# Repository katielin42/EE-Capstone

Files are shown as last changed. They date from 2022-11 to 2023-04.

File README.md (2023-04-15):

# EE-Capstone
This repository is the master collection of technical files (excluding reports and posters) for ECE490/491 group 1 capstone - Formula SAE EVCU (electric vehicle control unit) project. Group members are enrolled in electrical engineering at the U of A. Our valuable consultant and helpers are staff and instructors of ECE 490/491 as well as Le Minh Dang, a computer engineering student, all of whom are from the University of Alberta as well. 

## Hardware
Below is a high level hardware block diagram describing our fabricated PCB. Detailed 3d-view of the PCB and schematic can be found under Hardware Design/EVCU Rev B/EVCU. 



Design created by: Thomas Osei-Bonsu Jr. and Katie Lin

## Software
Below is a high level software flowchart block diagram describing our software control flow. Detailed Documentation about code can be found below. We are using STM32Cube IDE to develop our code currently, so our configuration for our software has mostly been STM32Cube IDE presets.



Design created by: Katie Lin and Thomas Osei-Bonsu Jr.

**Libraries/modules/middlewares we used:** 

+ **FreeRTOS**: for scheduling tasks and other parallel programming functionalities

+ **FATFS**: for communications and r/w functions with the SD card

**Current code structure**:

```STM32_test.ioc```: Settings file for pin configurations, turning peripherials on/off with STM32Cube IDE...etc.

```main.c```: pin defines, generation of global tasks/mutexes/threads and starting the kernel. Also imports all the other functions and runs them. 

```SD_task.c && SD_task.h```: calls functions to perform r/w functions to and from sd card, as well as mount/dismount...etc. 

```ADC_task.c && ADC_task.h```: processes values going into ADC pins and saves them in an intermediate buffer for further logic/processing. 

```CAN_task.c && CAN_task.h```: processes operations relevant to STM32 BxCAN functionalities, such as sending and receiving CAN messages, encoding and decoding of such messages...etc. 

```controller_task.c && controller_task.h```: a giant state machine with cases, interrupts...etc that links all the tasks together. Based on the inputs and outputs of the task files described above, decide the next steps of what the MCU needs to do, usually sending CAN messages and error logging upon error detection. 

## User Manual (for EVCU PCB)

![image](https://user-images.githubusercontent.com/47064869/232248181-f159828e-b120-455e-b322-5c2face49e1b.png)

Above is a physical image of the EVCU PCB. 

**Hardware Setup**

The setup for EVCU PCB should be done after reviewing the schematic and layout, which can be found under Hardware Design/EVCU Rev B/EVCU. For the EVCU PCB, provide a 12v DC input at J2 and ground signal. 

At J3, the APPS VPA/VPA2 and BSE sensor signal inputs to the ADC are labelled. Please consult the accelerator pedal datasheets to hook the APPS pedal/BSE sensors up correctly. 

The J5 DB9 connector is the CAN connector that can be hooked up to the motor controller. Our CAN bus speed is 0.5Mbit/second, so configure the motor controller accordingly. 

Before powering the board up, please ensure a microSD card is inserted and the sensors are powered and operational and connected to the analog inputs of this PCB. The current firmware will start running once the board is powered up. If any firmware errors occur, disconnect the PCB from power, ensure the hardware components are all connected, and reconnect the PCB to power. 

**Firmware Setup**

If one wishes to modify the firmware, please download STM32CubeIDE and clone this repository. The firmware project name in this repository is STM32_Test. Then, hook up serial wire debug pins in J1 to a debug programmer. These configurations can be found online. Then, clicking on the run or debug button will flash the updated code onto the EVCU PCB MCU. 

+ If the error conditions for the analog APPS/BSE sensors need to be modified, they can be changed in controller_task.c under the function check_error_condition(). Currently the code checks for APPS/BSE <0.5 or >4.5V as specified by the rules, but I believe the datasheet for one of the sensors says otherwise. 
+ If any CAN address/settings need to be modified, they can be changed in CAN_task.c

**Caveats**
+ If SD card logs aren't removed after powering off the board, they will be wiped at the next instance the board is powered up. 
+ SD card cannot be removed in the middle of operation. 
+ SD card might die due to too many writes, just replace a new micro SD card if you notice the EVCU firmware behaving weirdly with the SD card. 

**The code also works with the dev board. However, several changes need to be made in the .ioc**
+ uSD_detect pin needs to be changed from PC7 to PA5. 
+ Clock configurations need to be set: HSE from BYPASS to crystal/ceramic oscillator, and disable LSE. 
+ Connect the CAN transciever module to the dev board via the USB breakout board, connect to the non ST-Link microUSB input on the dev board (there are only two). 

Finally, save those changes to the .ioc file, close it, and flash the code onto the dev board.

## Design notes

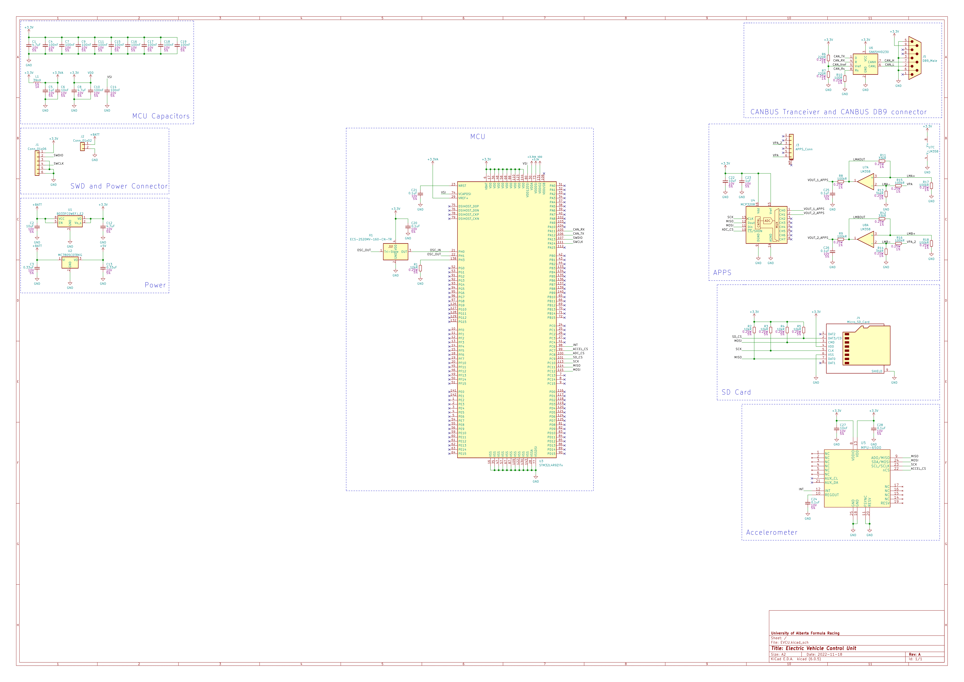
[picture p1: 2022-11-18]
Hardware Design/EVCU Rev B/EVCU.png

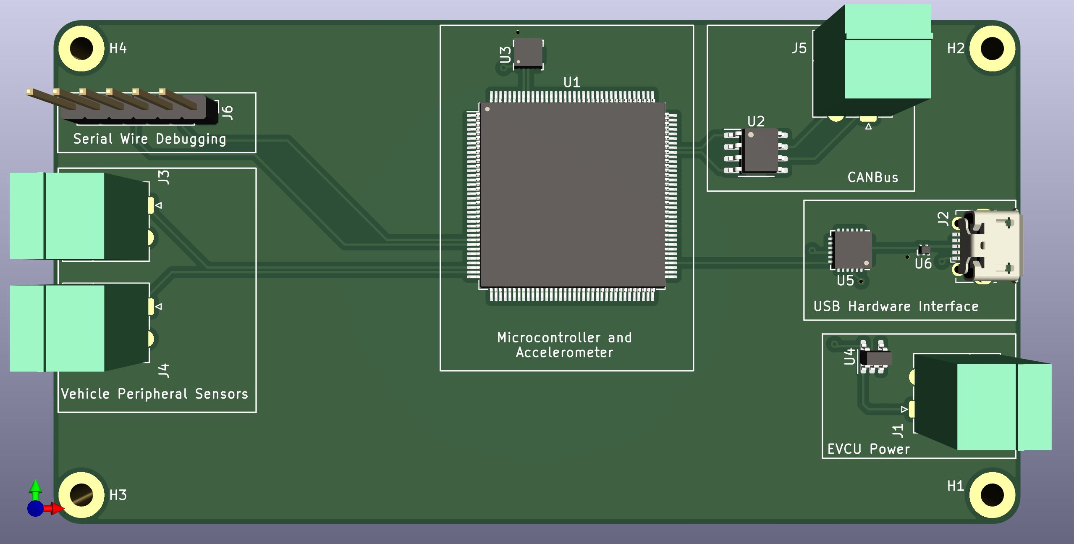
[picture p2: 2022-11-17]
3D Model/3DModelSpecificationsPictures/EVCUPic.png

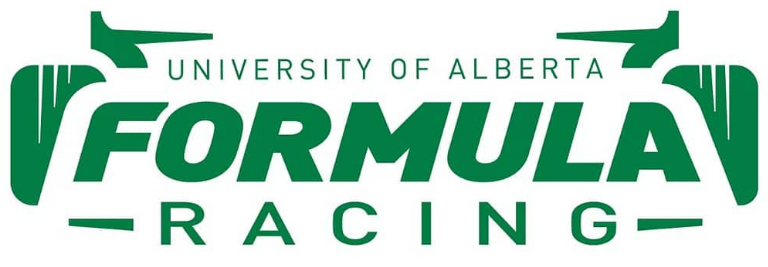
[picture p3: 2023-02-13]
3D Model/fsaepic.png

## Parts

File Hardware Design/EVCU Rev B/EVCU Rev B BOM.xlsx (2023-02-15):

Name | PCB Annotation | Value | Manufacturer | Mfr. P/N | Quantity | Description | Supplier | Supplier Link | Component Cost | Component Cost
STM32L4R9ZIT6 | U3 | IC MCU 32BIT 2MB FLASH 144LQFP | STMicroelectronics | STM32L4R9ZIT6 | 1 | ARM® Cortex®-M4 STM32L4R Microcontroller IC 32-Bit Single-Core 120MHz 2MB (2M x 8) FLASH 144-LQFP (20x20) | Digikey | https://www.digikey.ca/en/products/detail/stmicroelectronics/STM32L4R9ZIT6/7807676 | $35.44 | $118.61
AZ1117CR-3.3TRG1 | U1 | IC REG LINEAR 3.3V 1A SOT89 | Diodes Incorporated | AZ1117CR-3.3TRG1 | 1 | Linear Voltage Regulator IC Positive Fixed 1 Output 1A SOT-89-3 | Digikey | https://www.digikey.ca/en/products/detail/diodes-incorporated/AZ1117CR-3-3TRG1/4470988 | $0.69
AP62250WU-7 | U2 | DCDC CONV HV BUCK TSOT26 T&R 3K | Diodes Incorporated | AP62250WU-7 | 1 | Buck Switching Regulator IC Positive Adjustable 0.8V 1 Output 2.5A SOT-23-6 Thin, TSOT-23-6 | Digikey | https://www.digikey.ca/en/products/detail/diodes-incorporated/AP62250WU-7/12349212 | $0.77
ECS-2520MV-160-CN-TR | X1 | OSC XO 16.000MHZ CMOS SMD | ECS Inc. | ECS-2520MV-160-CN-TR | 1 | 16 MHz XO (Standard) HCMOS Oscillator 1.6V ~ 3.6V Enable/Disable 4-SMD, No Lead | Digikey | https://www.digikey.ca/en/products/detail/ecs-inc/ECS-2520MV-160-CN-TR/9742387 | $1.87
MPU-6500 | U5 | IMU ACCEL/GYRO 3-AXIS I2C 24QFN | TDK InvenSense | MPU-6500 | 1 | Accelerometer, Gyroscope, 6 Axis Sensor I²C, SPI Output | Digikey | https://www.digikey.ca/en/products/detail/tdk-invensense/MPU-6500/4385412 | $14.28
SN65HVD230QD | U6 | IC TRANSCEIVER HALF 1/1 8SOIC | Texas Instruments | SN65HVD230QDR | 1 | 1/1 Transceiver Half CANbus 8-SOIC | Digikey | https://www.digikey.ca/en/products/detail/texas-instruments/SN65HVD230QDR/1574499 | $4.79
LMV321WG-7 | U4, U7, U8 | IC OPAMP GP 1 CIRCUIT SOT25 | Diodes Incorporated | LMV321WG-7 | 3 | General Purpose Amplifier 1 Circuit Rail-to-Rail SOT-25 | Digikey | https://www.digikey.ca/en/products/detail/diodes-incorporated/LMV321WG-7/2182582 | $6.41
ESDCAN24-2BLY | U9 | TVS DIODE 24VWM 40VC SOT23-3 | STMicroelectronics | ESDCAN24-2BLY | 1 | 40V Clamp 5.5A (8/20µs) Ipp Tvs Diode Surface Mount SOT-23-3 | Digikey | https://www.digikey.ca/en/products/detail/stmicroelectronics/ESDCAN24-2BLY/3661709 | $0.71
EMIF06-MSD02N16 | U10 | FILTER RC(PI) 45 OHM/20PF SMD | STMicroelectronics | EMIF06-MSD02N16 | 1 | RC (Pi) EMI Filter 2nd Order Low Pass 6 Channel R = 45Ohms, C = 20pF (Total) 16-UFDFN Exposed Pad | Digikey | https://www.digikey.ca/en/products/detail/stmicroelectronics/EMIF06-MSD02N16/2043592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 | $1.76
ESDALC6V1W5 | U11 | TVS DIODE 3VWM SOT323-5 | STMicroelectronics | ESDALC6V1W5 | 1 | Clamp Ipp Tvs Diode Surface Mount SOT-323-5 | Digikey | https://www.digikey.ca/en/products/detail/stmicroelectronics/ESDALC6V1W5/1037997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 | $0.79
PJA3405_R1_00001 | Q1 | SOT-23, MOSFET | Panjit International Inc. | PJA3405_R1_00001 | 1 | P-Channel 30 V 3.6A (Ta) 1.25W (Ta) Surface Mount SOT-23 | Digikey | https://www.digikey.ca/en/products/detail/panjit-international-inc/PJA3405-R1-00001/14660219 | $0.71
0287001.PXCN | F1 | FUSE AUTO 1A 32VDC BLADE | Littelfuse Inc. | 0287001.PXCN | 1 | 1 A AC 32 V DC Fuse Automotive Requires Holder Blade, ATO/ATC | Digikey | https://www.digikey.ca/en/products/detail/littelfuse-inc/0287001-PXCN/3102551 | $0.48
3557_02 | F1 | FUSE BLOCK BLADE 500V 30A PCB | Keystone Electronics | 3557_02 | 1 | Fuse Block 30 A 500V 1 Circuit Blade Through Hole | Digikey | https://www.digikey.ca/en/products/detail/keystone-electronics/3557-2/2137305 | $2.09
SMBJ3V3-E3/5B | D1 | TVS DIODE 3.3VWM 10.3VC DO214AA | Vishay General Semiconductor - Diodes Division | SMBJ3V3-E3/5B | 1 | 10.3V Clamp 200A (8/20µs) Ipp Tvs Diode Surface Mount DO-214AA (SMBJ) | Digikey | https://www.digikey.ca/en/products/detail/vishay-general-semiconductor-diodes-division/SMBJ3V3-E3-5B/2147834 | $0.76
VJ0603Y104JXQPW1BC | C4, C7, C9, C10, C11, C15, C16, C17, C18, C19, C22, C31, C33, C20, C24, C25, C26, C28, C29, C30 | CAP CER 0.1UF 10V X7R 0603 | Vishay Vitramon | VJ0603Y104JXQPW1BC | 21 | 0.1 µF ±5% 10V Ceramic Capacitor X7R 0603 (1608 Metric) | Digikey | https://www.digikey.ca/en/products/detail/vishay-vitramon/VJ0603Y104JXQPW1BC/8305311 | $5.48
CL10A475KP8NNNC | C1, C8 | CAP CER 4.7UF 10V X5R 0603 | Samsung Electro-Mechanics | CL10A475KP8NNNC | 2 | 4.7 µF ±10% 10V Ceramic Capacitor X5R 0603 (1608 Metric) | Digikey | https://www.digikey.ca/en/products/detail/samsung-electro-mechanics/CL10A475KP8NNNC/3886702 | $1.70
CL31A106MBHNNNE | C3 | CAP CER 10UF 50V X5R 1206 | Samsung Electro-Mechanics | CL31A106MBHNNNE | 1 | 10 µF ±20% 50V Ceramic Capacitor X5R 1206 (3216 Metric) | Digikey | https://www.digikey.ca/en/products/detail/samsung-electro-mechanics/CL31A106MBHNNNE/5961220 | $2.69
CL10A106MA8NRNC | C2 | 10 µF ±20% 25V Ceramic Capacitor X5R 0603 (1608 Metric) | Samsung Electro-Mechanics | CL10A106MA8NRNC | 1 | 10 µF ±20% 25V Ceramic Capacitor X5R 0603 (1608 Metric) | Digikey | https://www.digikey.ca/en/products/detail/samsung-electro-mechanics/CL10A106MA8NRNC/3887527 | $2.58
CL10B105KP8NNNC | C5, C32 | CAP CER 1UF 10V X7R 0603 | Samsung Electro-Mechanics | CL10B105KP8NNNC | 2 | 1 µF ±10% 10V Ceramic Capacitor X7R 0603 (1608 Metric) | Digikey | https://www.digikey.ca/en/products/detail/samsung-electro-mechanics/CL10B105KP8NNNC/3887604 | $0.55
C1608X5R1A226M080AC | C13, C23, C12 | CAP CER 22UF 10V X5R 0603 | TDK Corporation | C1608X5R1A226M080AC | 3 | 22 µF ±20% 10V Ceramic Capacitor X5R 0603 (1608 Metric) | Digikey | https://www.digikey.ca/en/products/detail/tdk-corporation/C1608X5R1A226M080AC/3661560 | $4.51
GRM188R71A225KE15D | C14 | CAP CER 2.2UF 10V X7R 0603 | Murata Electronics | GRM188R71A225KE15D | 1 | 2.2 µF ±10% 10V Ceramic Capacitor X7R 0603 (1608 Metric) | Digikey | https://www.digikey.ca/en/products/detail/murata-electronics/GRM188R71A225KE15D/1033256 | $1.41
885012206014 | C6, C27 | CAP CER 10000PF 10V X7R 0603 | Würth Elektronik | 885012206014 | 2 | 10000 pF ±10% 10V Ceramic Capacitor X7R 0603 (1608 Metric) | Digikey | https://www.digikey.ca/en/products/detail/w%C3%BCrth-elektronik/885012206014/5453788 | $0.33
36502C39NJTDG | L1 | FIXED IND 100NH 8A 8 MOHM SMD | TDK Corporation | TFM322512ALMAR10MTAA | 1 | 100 nH Unshielded Thin Film Inductor 8 A 8mOhm Max 1210 (3225 Metric) | Digikey | https://www.digikey.ca/en/products/detail/tdk-corporation/TFM322512ALMAR10MTAA/16754576 | $2.98
CIGT252010EH2R2MNE | L2 | FIXED IND 2.2UH 2.4A 80MOHM SMD | Samsung Electro-Mechanics | CIGT252010EH2R2MNE | 1 | 2.2 µH Unshielded Thin Film Inductor 2.4 A 80mOhm Max 1008 (2520 Metric) | Digikey | https://www.digikey.ca/en/products/detail/samsung-electro-mechanics/CIGT252010EH2R2MNE/7041252 | $0.80
RNCP0805FTD10K0 | R1, R3 | RES 10K OHM 1% 1/4W 0805 | Stackpole Electronics Inc | RNCP0805FTD10K0 | 2 | 10 kOhms ±1% 0.25W, 1/4W Chip Resistor 0805 (2012 Metric) Anti-Sulfur Thin Film | Digikey | https://www.digikey.ca/en/products/detail/stackpole-electronics-inc/RNCP0805FTD10K0/2240262 | $1.12
ERJ-6ENF5232V | R2 | RES SMD 52.3K OHM 1% 1/8W 0805 | Panasonic Electronic Components | ERJ-6ENF5232V | 1 | 52.3 kOhms ±1% 0.125W, 1/8W Chip Resistor 0805 (2012 Metric) Automotive AEC-Q200 Thick Film | Digikey | https://www.digikey.ca/en/products/detail/panasonic-electronic-components/ERJ-6ENF5232V/111615 | $1.41
RK73H2ATTD2200F | R6, R7 | RES 220 OHM 1% 1/4W 0805 | KOA Speer Electronics, Inc. | RK73H2ATTD2200F | 2 | 220 Ohms ±1% 0.25W, 1/4W Chip Resistor 0805 (2012 Metric) Automotive AEC-Q200, Moisture Resistant Thick Film | Digikey | https://www.digikey.ca/en/products/detail/koa-speer-electronics-inc/RK73H2ATTD2200F/10234286 | $0.60
AC0805FR-7W100KL | R5, R9, R12 | RES 100 KOHM 1% 1/4W 0805 | YAGEO | AC0805FR-7W100KL | 9 | 100 kOhms ±1% 0.25W, 1/4W Chip Resistor 0805 (2012 Metric) Automotive AEC-Q200, Moisture Resistant Thick Film | Digikey | https://www.digikey.ca/en/products/detail/yageo/AC0805FR-7W100KL/12698912 | $1.14
RNCP0805FTD100R | R10 | RES 100 OHM 1% 1/4W 0805 | Stackpole Electronics Inc | RNCP0805FTD100R | 1 | 100 Ohms ±1% 0.25W, 1/4W Chip Resistor 0805 (2012 Metric) Anti-Sulfur Thin Film | Digikey | https://www.digikey.ca/en/products/detail/stackpole-electronics-inc/RNCP0805FTD100R/2240209 | $1.12
RC0805JR-0751KL | R4, R11, R8 | RES 51K OHM 5% 1/8W 0805 | YAGEO | RC0805JR-0751KL | 3 | 51 kOhms ±5% 0.125W, 1/8W Chip Resistor 0805 (2012 Metric) Moisture Resistant Thick Film | Digikey | https://www.digikey.ca/en/products/detail/yageo/RC0805JR-0751KL/728346 | $0.43
RK73B2ATTD121J | R19 | RES 120 OHM 5% 1/4W 0805 | KOA Speer Electronics, Inc. | RK73B2ATTD121J | 1 | 120 Ohms ±5% 0.25W, 1/4W Chip Resistor 0805 (2012 Metric) Automotive AEC-Q200 Thick Film | Digikey | https://www.digikey.ca/en/products/detail/koa-speer-electronics-inc/RK73B2ATTD121J/10236600 | $0.49
PPPC061LFBN-RC | J1 | CONN HDR 6POS 0.1 GOLD PCB | Sullins Connector Solutions | PPPC061LFBN-RC | 2 | 6 Position Header Connector 0.100" (2.54mm) Through Hole Gold | Digikey | https://www.digikey.ca/en/products/detail/sullins-connector-solutions/PPPC061LFBN-RC/810178 | $1.52
1984659 | J3 | TERM BLK 6POS SIDE ENT 3.5MM PCB | Phoenix Contact | 1984659 | 1 | 6 Position Wire to Board Terminal Block Horizontal with Board 0.138" (3.50mm) Through Hole | Digikey | https://www.digikey.ca/en/products/detail/phoenix-contact/1984659/950852 | $5.08
61300211121 | J6 | CONN HEADER VERT 2POS 2.54MM | Würth Elektronik | 61300211121 | 1 | Connector Header Through Hole 2 position 0.100" (2.54mm) | Digikey | https://www.digikey.ca/en/products/detail/w%C3%BCrth-elektronik/61300211121/4846823 | $1.63
1984617 | J2 | TERM BLK 2POS SIDE ENT 3.5MM PCB | Phoenix Contact | 1984617 | 2 | 2 Position Wire to Board Terminal Block Horizontal with Board 0.138" (3.50mm) Through Hole | Digikey | https://www.digikey.ca/en/products/detail/phoenix-contact/1984617/950849 | $3.44
693072010801 | J4 | CONN MICRO SD CARD HINGED TYPE | Würth Elektronik | 693072010801 | 1 | 8 Position Card Connector Secure Digital - microSD™ Surface Mount, Right Angle Gold | Digikey | https://www.digikey.ca/en/products/detail/w%C3%BCrth-elektronik/693072010801/3124584 | $4.91
A-DS 09 A/KG-T4S | J5 | CONN D-SUB PLUG 9POS R/A SLDR | Assmann WSW Components | A-DS 09 A/KG-T4S | 1 | 9 Position D-Sub Plug, Male Pins Connector | Digikey | https://www.digikey.ca/en/products/detail/assmann-wsw-components/A-DS-09-A-KG-T4S/1241806 | $1.14

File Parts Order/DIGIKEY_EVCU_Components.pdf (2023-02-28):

Please wait...

If this message is not eventually replaced by the proper contents of the document, your PDF viewer may not be able to display this type of document.

You can upgrade to the latest version of Adobe Reader for Windows®, Mac, or Linux® by visiting http://www.adobe.com/go/reader_download.

For more assistance with Adobe Reader visit http://www.adobe.com/go/acrreader.

Windows is either a registered trademark or a trademark of Microsoft Corporation in the United States and/or other countries. Mac is a trademark of Apple Inc., registered in the United States and other countries. Linux is the registered trademark of Linus Torvalds in the U.S. and other countries.

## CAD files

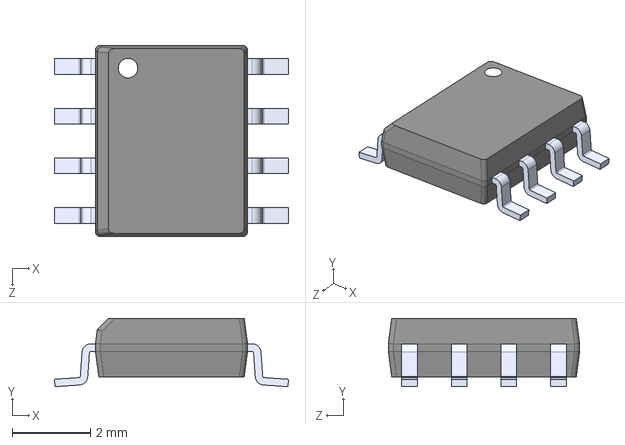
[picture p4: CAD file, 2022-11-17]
Hardware Design/KiCAD Custom Symbol Libraries/CAN-SN65HVD230/SN65HVD230.step
5.99 x 1.75 x 4.90 mm

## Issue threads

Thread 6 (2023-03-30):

ADC Value Scaling

katielin42, 2023-03-30:
Need to rescale ADC value from voltage divider 0-3.3v back to 0-5v

katielin42, 2023-04-10:
implemented fix, closing now

Closed 2023-04-10.

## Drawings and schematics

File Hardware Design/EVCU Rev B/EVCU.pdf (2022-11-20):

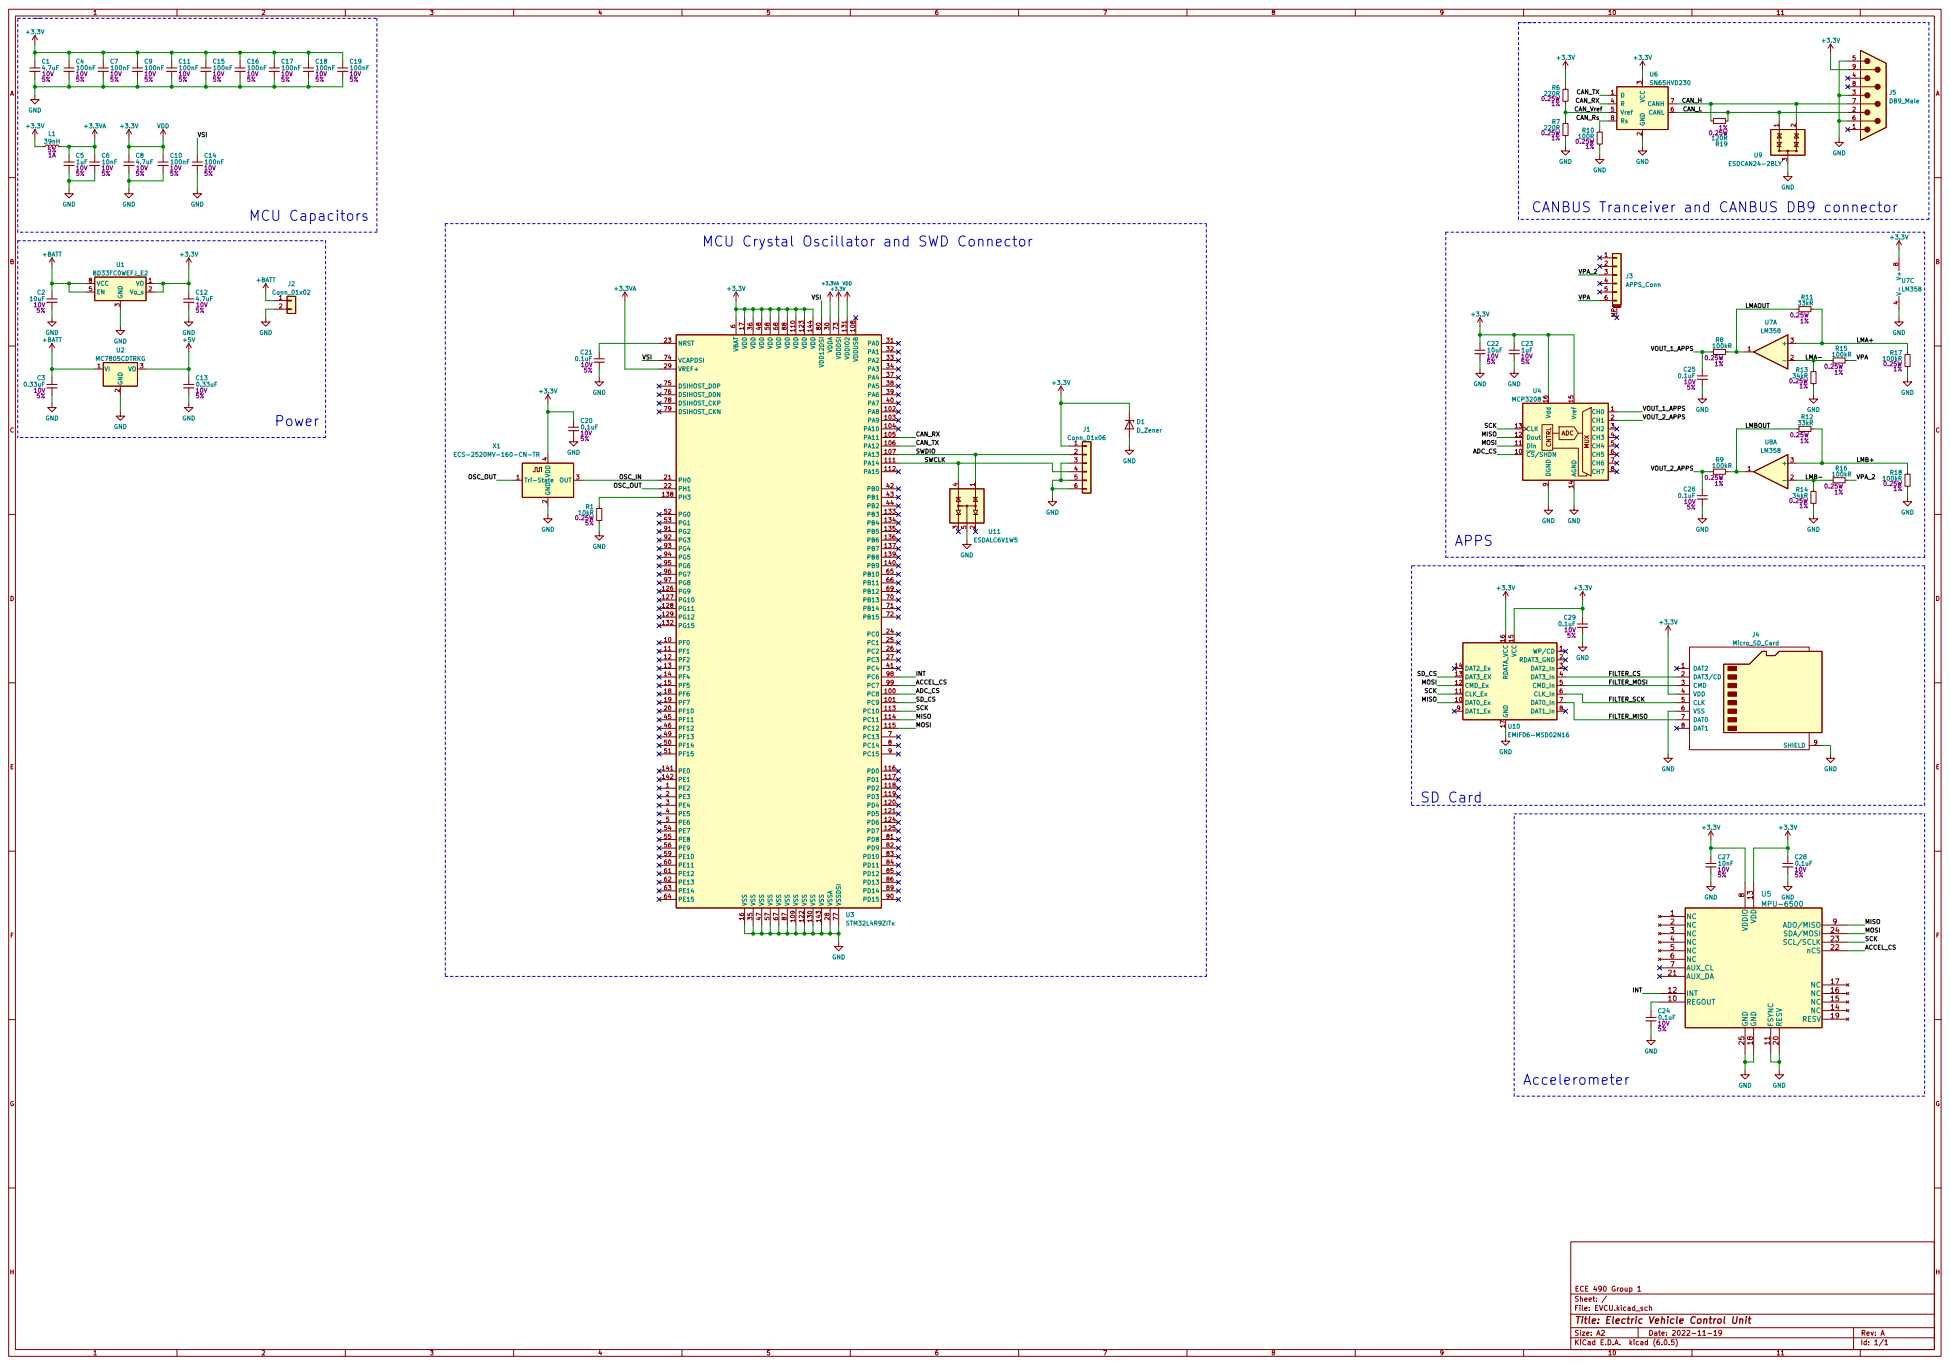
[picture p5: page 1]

CANBUS Tranceiver and CANBUS DB9 connector

MCU Crystal Oscillator and SWD Connector

File: EVCU.kicad_sch Sheet: / ECE 490 Group 1

Id: 1/1 Title: Electric Vehicle Control Unit

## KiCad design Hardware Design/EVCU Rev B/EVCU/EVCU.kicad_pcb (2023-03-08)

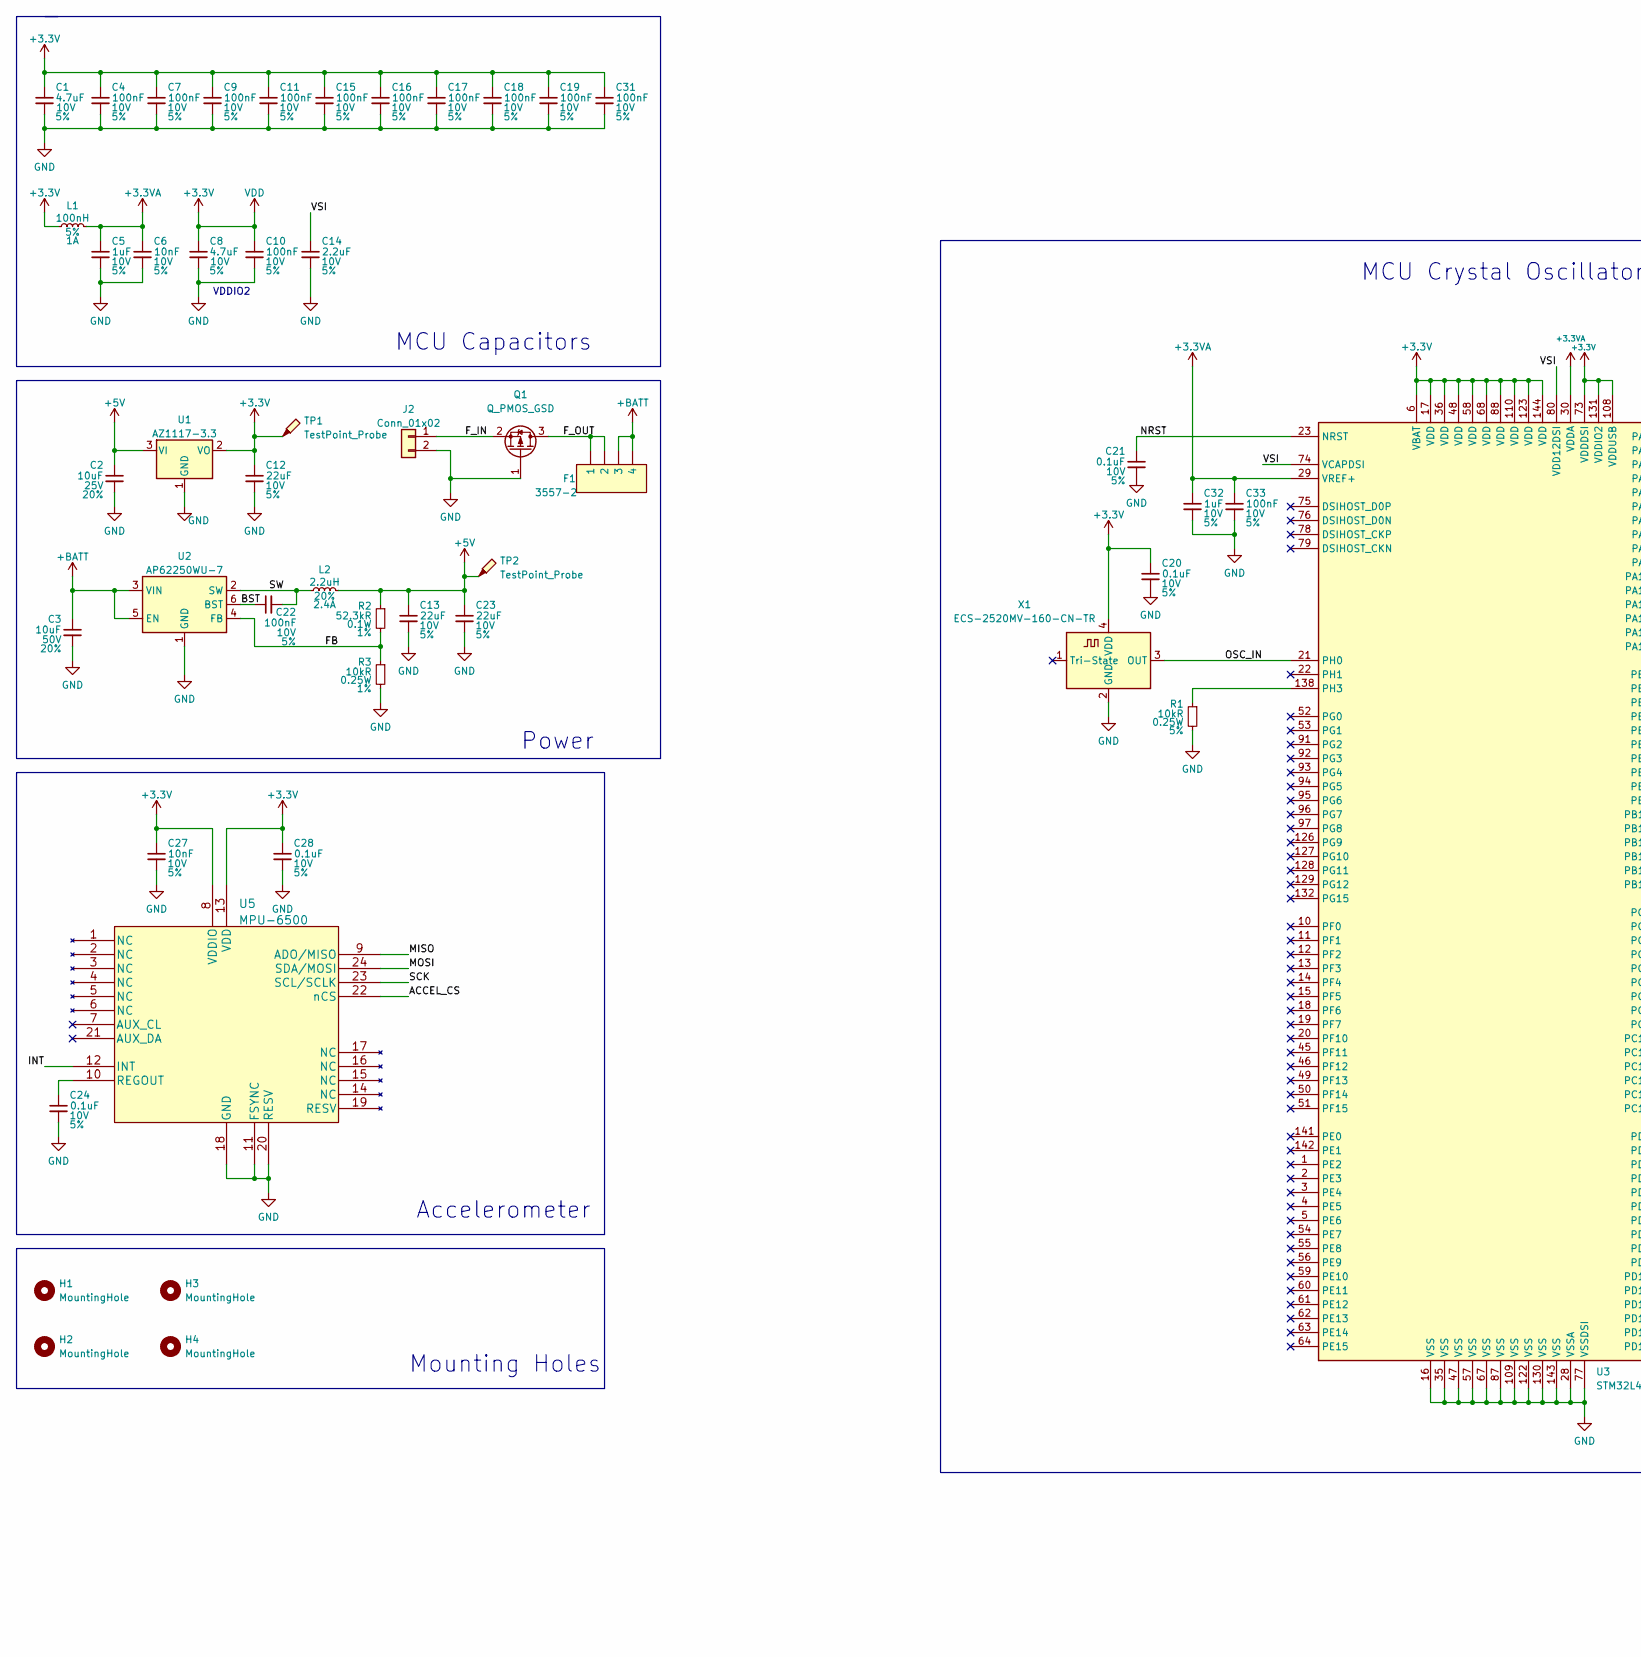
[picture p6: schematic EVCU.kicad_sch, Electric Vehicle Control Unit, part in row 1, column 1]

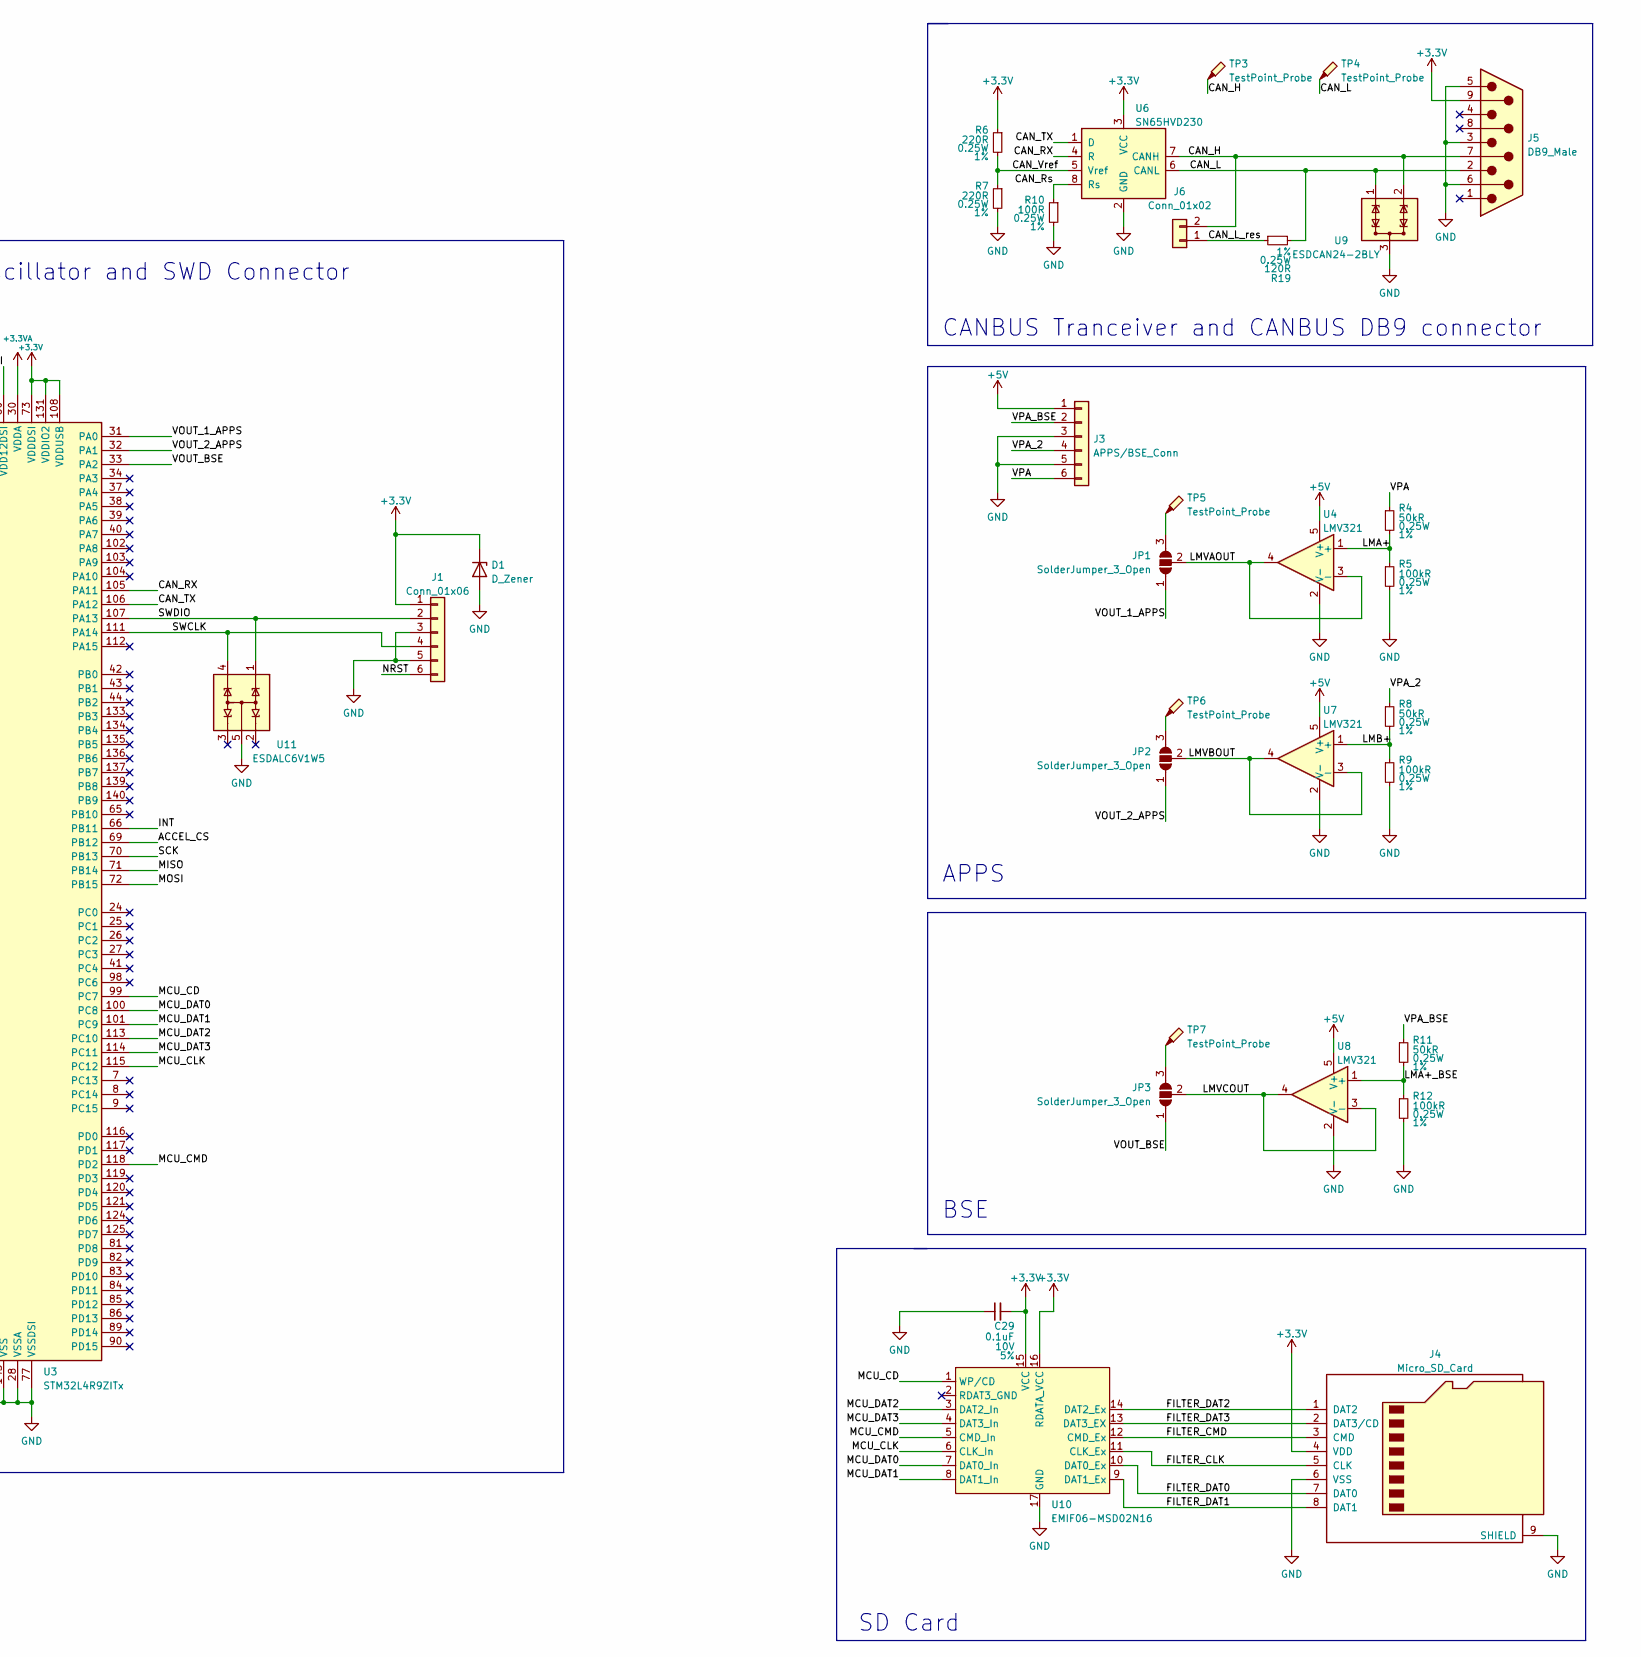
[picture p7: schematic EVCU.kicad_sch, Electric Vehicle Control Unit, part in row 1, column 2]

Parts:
C1, C8: 4.7uF; C_0603_1608Metric_Pad1.08x0.95mm_HandSolder; Tolerance 5%; Rating 10V
C2: 10uF; C_0603_1608Metric_Pad1.08x0.95mm_HandSolder; Rating 25V; Tolerance 20%
C3: 10uF; C_1206_3216Metric_Pad1.33x1.80mm_HandSolder; Rating 50V; Tolerance 20%
C4, C7, C9, C10, C11, C15, C16, C17, C18, C19, C22, C31, C33: 100nF; C_0603_1608Metric_Pad1.08x0.95mm_HandSolder; Rating 10V; Tolerance 5%
C5, C32: 1uF; C_0603_1608Metric_Pad1.08x0.95mm_HandSolder; Rating 10V; Tolerance 5%
C6, C27: 10nF; C_0603_1608Metric_Pad1.08x0.95mm_HandSolder; Rating 10V; Tolerance 5%
C12, C13, C23: 22uF; C_0603_1608Metric_Pad1.08x0.95mm_HandSolder; Rating 10V; Tolerance 5%
C14: 2.2uF; C_0603_1608Metric_Pad1.08x0.95mm_HandSolder; Rating 10V; Tolerance 5%
C20, C21, C24, C28, C29: 0.1uF; C_0603_1608Metric_Pad1.08x0.95mm_HandSolder; Rating 10V; Tolerance 5%
D1: D_Zener; D_SMB
F1: 3557-2
H1, H2, H3, H4: MountingHole; MountingHole_2.2mm_M2_DIN965_Pad
J1: Conn_01x06; PinSocket_1x06_P2.54mm_Vertical
J2: Conn_01x02; TerminalBlock_Phoenix_PT-1,5-2-3.5-H_1x02_P3.50mm_Horizontal
J3: APPS/BSE_Conn; TerminalBlock_Phoenix_PT-1,5-6-3.5-H_1x06_P3.50mm_Horizontal
J4: Micro_SD_Card; microSD_HC_Wuerth_693072010801
J5: DB9_Male; DSUB-9_Male_Horizontal_P2.77x2.84mm_EdgePinOffset7.70mm_Hou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
J6: Conn_01x02; PinHeader_1x02_P2.54mm_Vertical
JP1, JP2, JP3: SolderJumper_3_Open; SolderJumper-3_P1.3mm_Open_Pad1.0x1.5mm_NumberLabels
L1: 100nH; L_1210_3225Metric_Pad1.42x2.65mm_HandSolder; Rating 1A; Tolerance 5%
L2: 2.2uH; L_1008_2520Metric_Pad1.43x2.20mm_HandSolder; Rating 2.4A; Tolerance 20%
Q1: Q_PMOS_GSD; SOT-23
R1: 10kR; R_0805_2012Metric_Pad1.20x1.40mm_HandSolder; Rating 0.25W; Tolerance 5%
R2: 52.3kR; R_0805_2012Metric_Pad1.20x1.40mm_HandSolder; Rating 0.1W; Tolerance 1%
R3: 10kR; R_0805_2012Metric_Pad1.20x1.40mm_HandSolder; Rating 0.25W; Tolerance 1%
R4, R8, R11: 50kR; R_0805_2012Metric_Pad1.20x1.40mm_HandSolder; Rating 0.25W; Tolerance 1%
R5, R9, R12: 100kR; R_0805_2012Metric_Pad1.20x1.40mm_HandSolder; Rating 0.25W; Tolerance 1%
R6, R7: 220R; R_0805_2012Metric_Pad1.20x1.40mm_HandSolder; Rating 0.25W; Tolerance 1%
R10: 100R; R_0805_2012Metric_Pad1.20x1.40mm_HandSolder; Rating 0.25W; Tolerance 1%
R19: 120R; R_0805_2012Metric_Pad1.20x1.40mm_HandSolder; Rating 0.25W; Tolerance 1%
TP1, TP2, TP3, TP4, TP5, TP6, TP7: TestPoint_Probe; TestPoint_Pad_1.5x1.5mm
U1: AZ1117-3.3; SOT-89-3_Handsoldering
U2: AP62250WU-7; TSOT-23-6_HandSoldering
U3: STM32L4R9ZITx; LQFP-144_20x20mm_P0.5mm
U4, U7, U8: LMV321; SOT-353_SC-70-5_Handsoldering
U5: MPU-6500; QFN-24_3x3mm_P0.4mm
U6: SN65HVD230; SOIC-8_3.9x4.9mm_P1.27mm
U9: ESDCAN24-2BLY; SC-59
U10: EMIF06-MSD02N16
U11: ESDALC6V1W5; SOT-353_SC-70-5_Handsoldering
X1: ECS-2520MV-160-CN-TR; Oscillator_SMD_ECS_2520MV-xxx-xx-4Pin_2.5x2.0mm

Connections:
+3.3VA: C5.1, C6.1, C32.1, C33.1, L1.2, U3.29 (VREF+), U3.30 (VDDA)
+3V3: C1.1, C4.1, C7.1, C8.1, C9.1, C10.1, C11.1, C12.1, C15.1, C16.1, C17.1, C18.1, C19.1, C20.1, C27.1, C28.1, C29.2, C31.1, D1.1 (K), J1.1, J4.4 (VDD), J5.9, L1.1, R6.1, TP1.1, U1.2 (VO), U3.6 (VBAT), U3.17 (VDD), U3.36 (VDD), U3.48 (VDD), U3.58 (VDD), U3.68 (VDD), U3.73 (VDDDSI), U3.88 (VDD), U3.108 (VDDUSB), U3.110 (VDD), U3.123 (VDD), U3.131 (VDDIO2), U3.144 (VDD), U5.8 (VDDIO), U5.13 (VDD), U6.3 (VCC), U10.15 (VCC), U10.16 (RDATA_VCC), X1.4 (VDD)
+5V: C2.1, C13.1, C23.1, J3.1, L2.2, R2.1, TP2.1, U1.3 (VI), U4.5 (V+), U7.5 (V+), U8.5 (V+)
+BATT: C3.1, F1., F1.3, F1.4, U2.3 (VIN), U2.5 (EN)
/ACCEL_CS: U3.69 (PB12), U5.22 (nCS)
/BST: C22.1, U2.6 (BST)
/CAN_H: J5.7, J6.2, TP3.1, U6.7 (CANH), U9.2
/CAN_L: J5.2, R19.2, TP4.1, U6.6 (CANL), U9.1
/CAN_L_res: J6.1, R19.1
/CAN_RX: U3.105 (PA11), U6.4 (R)
/CAN_Rs: R10.1, U6.8 (Rs)
/CAN_TX: U3.106 (PA12), U6.1 (D)
/CAN_Vref: R6.2, R7.1, U6.5 (Vref)
/FB: R2.2, R3.1, U2.4 (FB)
/FILTER_CLK: J4.5 (CLK), U10.11 (CLK_Ex)
/FILTER_CMD: J4.3 (CMD), U10.12 (CMD_Ex)
/FILTER_DAT0: J4.7 (DAT0), U10.10 (DAT0_Ex)
/FILTER_DAT1: J4.8 (DAT1), U10.9 (DAT1_Ex)
/FILTER_DAT2: J4.1 (DAT2), U10.14 (DAT2_Ex)
/FILTER_DAT3: J4.2 (DAT3/CD), U10.13 (DAT3_EX)
/F_IN: J2.1, Q1.2 (S)
/F_OUT: F1., F1.1, F1.2, Q1.3 (D)
/INT: U3.66 (PB11), U5.12 (INT)
/LMA+: R4.2, R5.1, U4.1 (+)
/LMA+_BSE: R11.2, R12.1, U8.1 (+)
/LMB+: R8.2, R9.1, U7.1 (+)
/LMVAOUT: JP1.2 (C), U4.3 (-), U4.4
/LMVBOUT: JP2.2 (C), U7.3 (-), U7.4
/LMVCOUT: JP3.2 (C), U8.3 (-), U8.4
/MCU_CD: U3.99 (PC7), U10.1 (WP/CD)
/MCU_CLK: U3.115 (PC12), U10.6 (CLK_In)
/MCU_CMD: U3.118 (PD2), U10.5 (CMD_In)
/MCU_DAT0: U3.100 (PC8), U10.7 (DAT0_In)
/MCU_DAT1: U3.101 (PC9), U10.8 (DAT1_In)
/MCU_DAT2: U3.113 (PC10), U10.3 (DAT2_In)
/MCU_DAT3: U3.114 (PC11), U10.4 (DAT3_In)
/MISO: U3.71 (PB14), U5.9 (ADO/MISO)
/MOSI: U3.72 (PB15), U5.24 (SDA/MOSI)
/NRST: C21.1, J1.6, U3.23 (NRST)
/OSC_IN: U3.21 (PH0), X1.3 (OUT)
/SCK: U3.70 (PB13), U5.23 (SCL/SCLK)
/SW: C22.2, L2.1, U2.2 (SW)
/SWCLK: J1.4, U3.111 (PA14), U11.4
/SWDIO: J1.2, U3.107 (PA13), U11.1
/VOUT_1_APPS: JP1.1 (A), U3.31 (PA0)
/VOUT_2_APPS: JP2.1 (A), U3.32 (PA1)
/VOUT_BSE: JP3.1 (A), U3.33 (PA2)
/VPA: J3.6, R4.1
/VPA_2: J3.4, R8.1
/VPA_BSE: J3.2, R11.1
/VSI: C14.1, U3.74 (VCAPDSI), U3.80 (VDD12DSI)
GND: C1.2, C2.2, C3.2, C4.2, C5.2, C6.2, C7.2, C8.2, C9.2, C10.2, C11.2, C12.2, C13.2, C14.2, C15.2, C16.2, C17.2, C18.2, C19.2, C20.2, C21.2, C23.2, C24.2, C27.2, C28.2, C29.1, C31.2, C32.2, C33.2, D1.2 (A), H1.1, H2.1, H3.1, H4.1, J1.3, J1.5, J2.2, J3.3, J3.5, J4.6 (VSS), J4.9 (SHIELD), J5.0, J5.3, J5.5, J5.6, Q1.1 (G), R1.2, R3.2, R5.2, R7.2, R9.2, R10.2, R12.2, U1.1 (GND), U2.1 (GND), U3.16 (VSS), U3.28 (VSSA), U3.35 (VSS), U3.47 (VSS), U3.57 (VSS), U3.67 (VSS), U3.77 (VSSDSI), U3.87 (VSS), U3.109 (VSS), U3.122 (VSS), U3.130 (VSS), U3.143 (VSS), U4.2 (V-), U5.11 (FSYNC), U5.18 (GND), U5.20 (RESV), U6.2 (GND), U7.2 (V-), U8.2 (V-), U9.3, U10.17 (GND), U11.5, X1.2 (GND)
unnamed: C24.1, U5.10 (REGOUT)
unnamed: JP1.3 (B), TP5.1
unnamed: JP2.3 (B), TP6.1
unnamed: JP3.3 (B), TP7.1
unnamed: R1.1, U3.138 (PH3)

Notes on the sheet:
Accelerometer
SD Card
Power
BSE
MCU Capacitors
VDDIO2
CANBUS Tranceiver and CANBUS DB9 connector
APPS
MCU Crystal Oscillator and SWD Connector
Mounting Holes

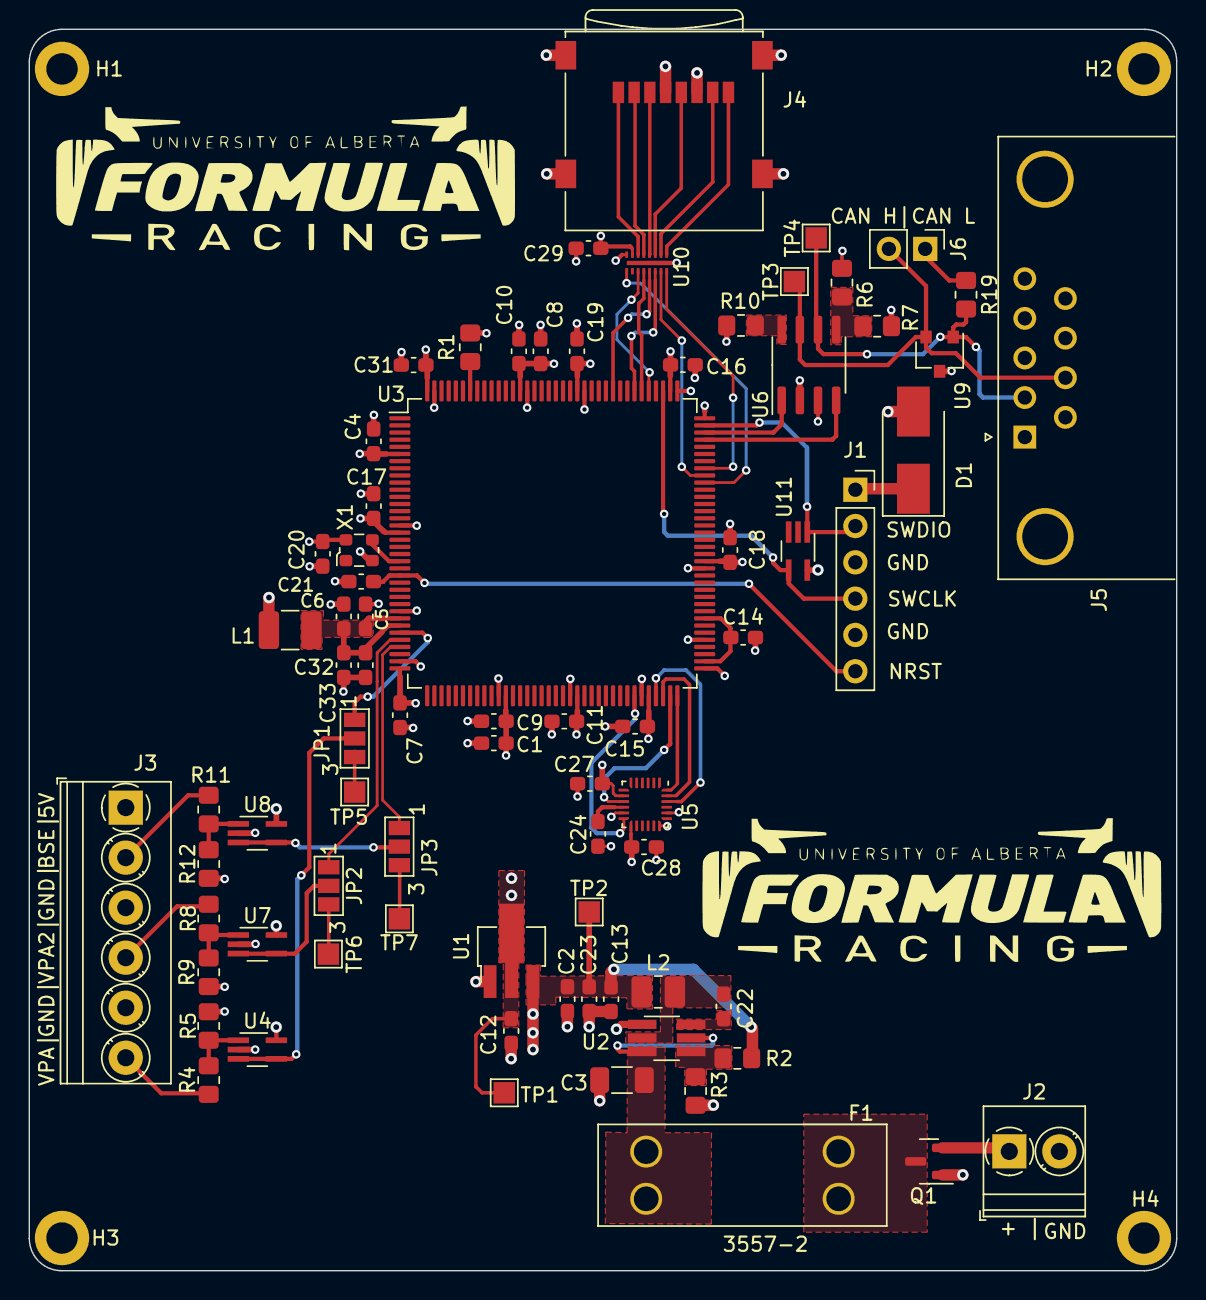
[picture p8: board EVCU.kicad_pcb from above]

Board: 4 copper layers, 80.3 x 86.8 mm, 80 parts (0 on the bottom side), 57 nets.

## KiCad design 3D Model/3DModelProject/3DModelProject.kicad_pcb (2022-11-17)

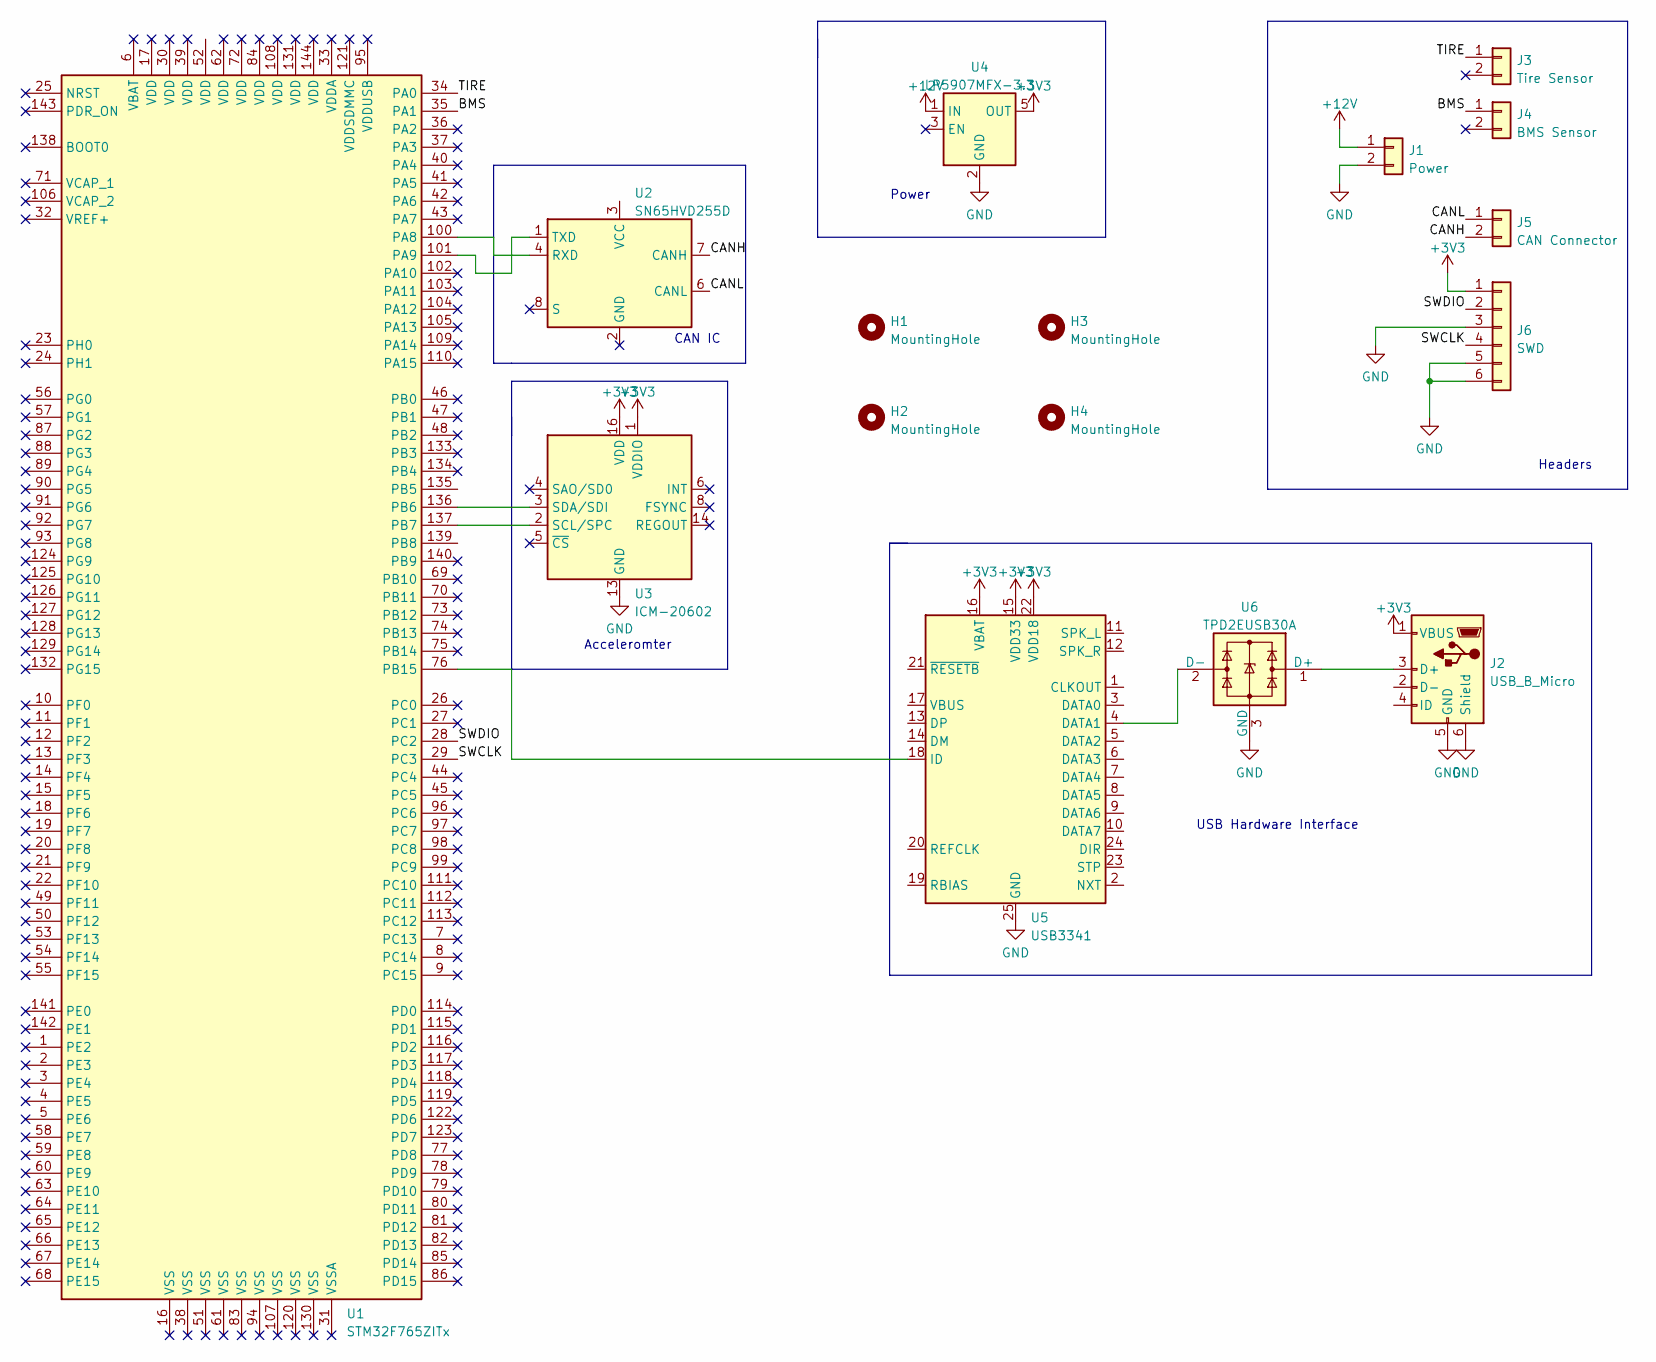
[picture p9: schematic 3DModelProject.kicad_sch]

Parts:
H1, H2, H3, H4: MountingHole; MountingHole_2.5mm_Pad_TopBottom
J1: Power; PhoenixContact_MC_1,5_2-G-3.5_1x02_P3.50mm_Horizontal
J2: USB_B_Micro; USB_Micro-B_Molex-105017-0001
J3: Tire Sensor; PhoenixContact_MC_1,5_2-G-3.5_1x02_P3.50mm_Horizontal
J4: BMS Sensor; PhoenixContact_MC_1,5_2-G-3.5_1x02_P3.50mm_Horizontal
J5: CAN Connector; PhoenixContact_MC_1,5_2-G-3.5_1x02_P3.50mm_Horizontal
J6: SWD; PinHeader_1x06_P2.54mm_Vertical
U1: STM32F765ZITx; LQFP-144_20x20mm_P0.5mm
U2: SN65HVD255D; SOIC-8_3.9x4.9mm_P1.27mm
U3: ICM-20602; LGA-16_3x3mm_P0.5mm_LayoutBorder3x5y
U4: LP5907MFX-3.3; SOT-23-5
U5: USB3341; QFN-24-1EP_4x4mm_P0.5mm_EP2.6x2.6mm
U6: TPD2EUSB30A; Texas_DRT-3

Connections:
+3V3: J2.1 (VBUS), J6.1, U3.1 (VDDIO), U3.16 (VDD), U4.5 (OUT), U5.15 (VDD33), U5.16 (VBAT), U5.22 (VDD18)
+12V: J1.1, U4.1 (IN)
/BMS: J4.1, U1.35 (PA1)
/CANH: J5.2, U2.7 (CANH)
/CANL: J5.1, U2.6 (CANL)
/SWCLK: J6.4, U1.29 (PC3)
/SWDIO: J6.2, U1.28 (PC2)
/TIRE: J3.1, U1.34 (PA0)
GND: J1.2, J2.5 (GND), J2.6 (Shield), J6.3, J6.5, J6.6, U3.9 (GND), U3.10 (GND), U3.11 (GND), U3.12 (GND), U3.13 (GND), U3.15 (GND), U4.2 (GND), U5.25 (GND), U6.3 (GND)
unnamed: J2.3 (D+), U6.1 (D+)
unnamed: U1.76 (PB15), U5.18 (ID)
unnamed: U1.100 (PA8), U2.4 (RXD)
unnamed: U1.101 (PA9), U2.1 (TXD)
unnamed: U1.136 (PB6), U3.3 (SDA/SDI)
unnamed: U1.137 (PB7), U3.2 (SCL/SPC)
unnamed: U5.4 (DATA1), U6.2 (D-)

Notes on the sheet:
CAN IC
USB Hardware Interface
Headers
Acceleromter
Power

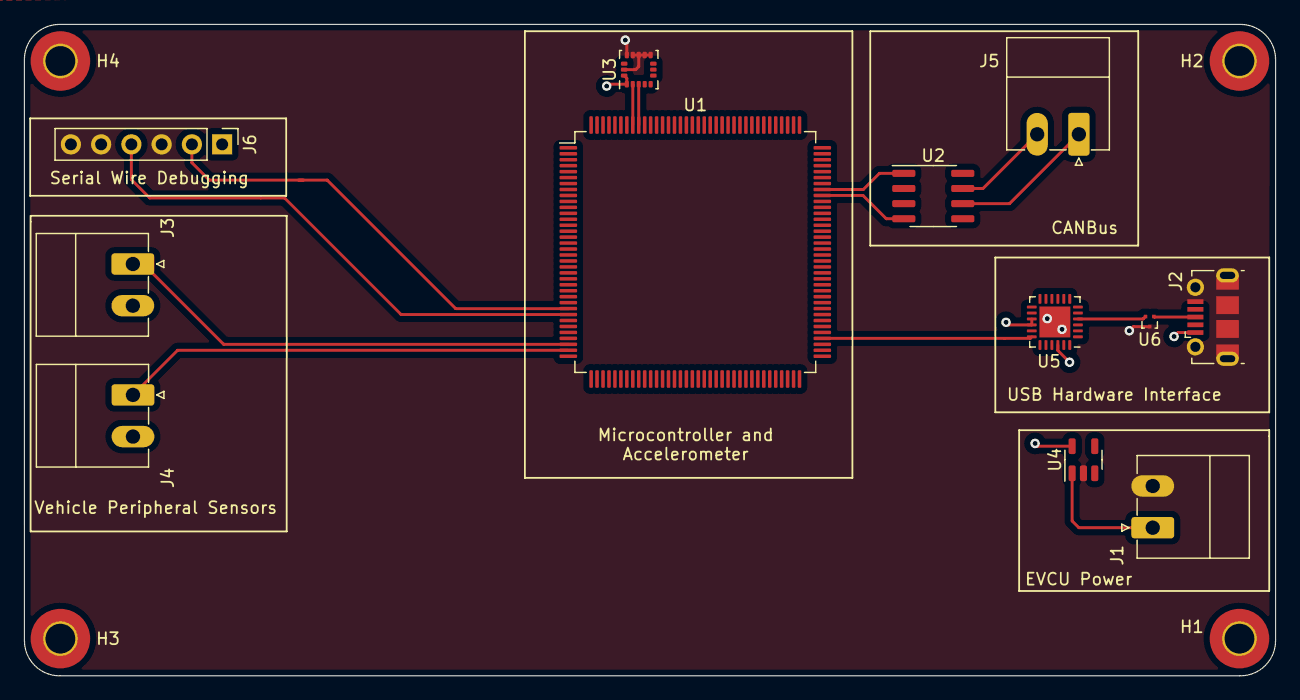
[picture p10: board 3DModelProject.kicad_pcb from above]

Board: 4 copper layers, 105.1 x 54.7 mm, 16 parts (0 on the bottom side), 16 nets.

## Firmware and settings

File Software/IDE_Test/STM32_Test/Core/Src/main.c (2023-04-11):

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
/* Includes ------------------------------------------------------------------*/
#include "main.h"
#include "cmsis_os.h"
#include "fatfs.h"

/* USER CODE BEGIN Includes */
#include "adc_task.h"
#include "sd_task.h"
#include "controller_task.h"
#include "can_task.h"
/* USER CODE END Includes */

/* USER CODE BEGIN PM */
///user defined variables///



/* USER CODE END PM */

ADC_HandleTypeDef hadc1;
DMA_HandleTypeDef hdma_adc1;

CAN_HandleTypeDef hcan1;

SD_HandleTypeDef hsd1;

/* Definitions for defaultTask */
osThreadId_t defaultTaskHandle;
const osThreadAttr_t defaultTask_attributes = {
  .name = "defaultTask",
  .stack_size = 128 * 4,
  .priority = (osPriority_t) osPriorityNormal,
};
/* USER CODE BEGIN PV */

/* Definitions for myMutex01 */
/* Definitions for threads */

//osThreadId_t thr_2;
//const osThreadAttr_t thr_2_attributes = {
//  .name = "defaultTask",
//  .stack_size = 128 * 4,
//  .priority = (osPriority_t) osPriorityNormal,
//};
/* USER CODE END PV */

void SystemClock_Config(void);
static void MX_GPIO_Init(void);
static void MX_DMA_Init(void);
static void MX_SDMMC1_SD_Init(void);
static void MX_CAN1_Init(void);
static void MX_ADC1_Init(void);
void StartDefaultTask(void *argument);

/**
  * @brief  The application entry point.
  * @retval int
  */
int main(void)
{
  /* MCU Configuration--------------------------------------------------------*/

  /* Reset of all peripherals, Initializes the Flash interface and the Systick. */
  HAL_Init();

  /* Configure the system clock */
  SystemClock_Config();

  /* Initialize all configured peripherals */
  MX_GPIO_Init();
  MX_DMA_Init();
  MX_SDMMC1_SD_Init();
  MX_CAN1_Init();
  MX_ADC1_Init();
  MX_FATFS_Init();
  /* Init scheduler */
  osKernelInitialize();

  /* USER CODE BEGIN RTOS_MUTEX */
  /* add mutexes, ... */
  /* USER CODE END RTOS_MUTEX */

  /* USER CODE BEGIN RTOS_SEMAPHORES */
  /* add semaphores, ... */
  /* USER CODE END RTOS_SEMAPHORES */

  /* USER CODE BEGIN RTOS_TIMERS */
  /* start timers, add new ones, ... */
  /* USER CODE END RTOS_TIMERS */

  /* USER CODE BEGIN RTOS_QUEUES */
  /* add queues, ... */

  /* USER CODE END RTOS_QUEUES */

  /* Create the thread(s) */
  /* creation of defaultTask */
  defaultTaskHandle = osThreadNew(StartDefaultTask, NULL, &defaultTask_attributes);

  /* USER CODE BEGIN RTOS_THREADS */
  /* Initialize user threads ... */
  ADC_Init(&hadc1);
  can_Init();
  state_machine_init();
  /* USER CODE END RTOS_THREADS */

  /* USER CODE BEGIN RTOS_EVENTS */
  /* add events, ... */
  /* USER CODE END RTOS_EVENTS */

  /* Start scheduler */
  osKernelStart();

  /* We should never get here as control is now taken by the scheduler */
  /* Infinite loop */
  /* USER CODE BEGIN WHILE */
  while (1)
  {
    /* USER CODE END WHILE */

    /* USER CODE BEGIN 3 */
  }
  /* USER CODE END 3 */
}

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
/* USER CODE BEGIN Header_StartDefaultTask */
/**
  * @brief  Function implementing the defaultTask thread.
  * @param  argument: Not used
  * @retval None
  */
/* USER CODE END Header_StartDefaultTask */
void StartDefaultTask(void *argument)
{
  /* USER CODE BEGIN 5 */
  for(;;)
  {
    osDelay(1);
  }
  /* USER CODE END 5 */
}

/**
  * @brief  Period elapsed callback in non blocking mode
  * @note   This function is called  when TIM6 interrupt took place, inside
  * HAL_TIM_IRQHandler(). It makes a direct call to HAL_IncTick() to increment
  * a global variable "uwTick" used as application time base.
  * @param  htim : TIM handle
  * @retval None
  */
void HAL_TIM_PeriodElapsedCallback(TIM_HandleTypeDef *htim)
{
  if (htim->Instance == TIM6) {
    HAL_IncTick();
  }
}

/**
  * @brief  This function is executed in case of error occurrence.
  * @retval None
  */
void Error_Handler(void)
{
  /* USER CODE BEGIN Error_Handler_Debug */
  /* User can add his own implementation to report the HAL error return state */
  __disable_irq();
  while (1)
  {
  }
  /* USER CODE END Error_Handler_Debug */
}

#ifdef  USE_FULL_ASSERT
/**
  * @brief  Reports the name of the source file and the source line number
  *         where the assert_param error has occurred.
  * @param  file: pointer to the source file name
  * @param  line: assert_param error line source number
  * @retval None
  */
void assert_failed(uint8_t *file, uint32_t line)
{
  /* USER CODE BEGIN 6 */
  /* User can add his own implementation to report the file name and line number,
     ex: printf("Wrong parameters value: file %s on line %d\r\n", file, line) */
  /* USER CODE END 6 */
}
#endif /* USE_FULL_ASSERT */

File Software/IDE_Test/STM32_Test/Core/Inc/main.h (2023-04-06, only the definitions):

#define OCTOSPIM_P2_IO1_Pin GPIO_PIN_10
#define OCTOSPIM_P2_IO1_GPIO_Port GPIOI
#define MIC_VDD_Pin GPIO_PIN_2
#define MIC_VDD_GPIO_Port GPIOH
#define PSRAM_NBL0_Pin GPIO_PIN_0
#define PSRAM_NBL0_GPIO_Port GPIOE
#define ARD_D6_Pin GPIO_PIN_4
#define ARD_D6_GPIO_Port GPIOB
#define SWO_Pin GPIO_PIN_3
#define SWO_GPIO_Port GPIOB
#define USART3_RTS_Pin GPIO_PIN_15
#define USART3_RTS_GPIO_Port GPIOA
#define SWCLK_Pin GPIO_PIN_14
#define SWCLK_GPIO_Port GPIOA
#define SWDIO_Pin GPIO_PIN_13
#define SWDIO_GPIO_Port GPIOA
#define ARD_10_Pin GPIO_PIN_0
#define ARD_10_GPIO_Port GPIOI
#define DSI_SPI_USART_CS_Pin GPIO_PIN_14
#define DSI_SPI_USART_CS_GPIO_Port GPIOH
#define DCMI_D7_Pin GPIO_PIN_7
#define DCMI_D7_GPIO_Port GPIOI
#define PSRAM_NBL1_Pin GPIO_PIN_1
#define PSRAM_NBL1_GPIO_Port GPIOE
#define SAI1_SDB_Pin GPIO_PIN_5
#define SAI1_SDB_GPIO_Port GPIOB
#define OCTOSPIM_P2_IO6_Pin GPIO_PIN_9
#define OCTOSPIM_P2_IO6_GPIO_Port GPIOG
#define D2_Pin GPIO_PIN_0
#define D2_GPIO_Port GPIOD
#define OCTOSPIM_P2_CLK_Pin GPIO_PIN_6
#define OCTOSPIM_P2_CLK_GPIO_Port GPIOI
#define MFX_IRQ_OUT_Pin GPIO_PIN_1
#define MFX_IRQ_OUT_GPIO_Port GPIOI
#define DCMI_D3_Pin GPIO_PIN_12
#define DCMI_D3_GPIO_Port GPIOH
#define OCTOSPIM_P2_IO0_Pin GPIO_PIN_11
#define OCTOSPIM_P2_IO0_GPIO_Port GPIOI
#define I2C1_SCL_Pin GPIO_PIN_6
#define I2C1_SCL_GPIO_Port GPIOB
#define OCTOSPIM_P2_DQS_Pin GPIO_PIN_15
#define OCTOSPIM_P2_DQS_GPIO_Port GPIOG
#define PSRAM_OE_Pin GPIO_PIN_4
#define PSRAM_OE_GPIO_Port GPIOD
#define D3_Pin GPIO_PIN_1
#define D3_GPIO_Port GPIOD
#define ARD_D9_Pin GPIO_PIN_13
#define ARD_D9_GPIO_Port GPIOH
#define OCTOPSIM_P2_IO4_Pin GPIO_PIN_9
#define OCTOPSIM_P2_IO4_GPIO_Port GPIOH
#define PSRAM_A20_Pin GPIO_PIN_4
#define PSRAM_A20_GPIO_Port GPIOE
#define PSRAM_A19_Pin GPIO_PIN_3
#define PSRAM_A19_GPIO_Port GPIOE
#define SAI1_MCKA_Pin GPIO_PIN_2
#define SAI1_MCKA_GPIO_Port GPIOE
#define SAI1_FSA_Pin GPIO_PIN_9
#define SAI1_FSA_GPIO_Port GPIOB
#define PSRAM_ADV_Pin GPIO_PIN_7
#define PSRAM_ADV_GPIO_Port GPIOB
#define OCTOSPIM_P2_IO7_Pin GPIO_PIN_10
#define OCTOSPIM_P2_IO7_GPIO_Port GPIOG
#define PSRAM_WE_Pin GPIO_PIN_5
#define PSRAM_WE_GPIO_Port GPIOD
#define uSD_CMD_Pin GPIO_PIN_2
#define uSD_CMD_GPIO_Port GPIOD
#define uSD_D2_Pin GPIO_PIN_10
#define uSD_D2_GPIO_Port GPIOC
#define DCMI_D5_Pin GPIO_PIN_4
#define DCMI_D5_GPIO_Port GPIOI
#define USB_OTGFS_ID_Pin GPIO_PIN_10
#define USB_OTGFS_ID_GPIO_Port GPIOA
#define JOY_SEL_Pin GPIO_PIN_13
#define JOY_SEL_GPIO_Port GPIOC
#define SAI1_SDA_Pin GPIO_PIN_6
#define SAI1_SDA_GPIO_Port GPIOE
#define SAI1_SCKA_Pin GPIO_PIN_5
#define SAI1_SCKA_GPIO_Port GPIOE
#define PSRAM_WAIT_Pin GPIO_PIN_6
#define PSRAM_WAIT_GPIO_Port GPIOD
#define PSRAM_CLK_Pin GPIO_PIN_3
#define PSRAM_CLK_GPIO_Port GPIOD
#define uSD_D3_Pin GPIO_PIN_11
#define uSD_D3_GPIO_Port GPIOC
#define DCMI_VSYNC_Pin GPIO_PIN_5
#define DCMI_VSYNC_GPIO_Port GPIOI
#define PSRAM_A2_Pin GPIO_PIN_2
#define PSRAM_A2_GPIO_Port GPIOF
#define PSRAM_A1_Pin GPIO_PIN_1
#define PSRAM_A1_GPIO_Port GPIOF
#define PSRAM_A0_Pin GPIO_PIN_0
#define PSRAM_A0_GPIO_Port GPIOF
#define OCTOSPIM_P2_CS_Pin GPIO_PIN_12
#define OCTOSPIM_P2_CS_GPIO_Port GPIOG
#define PSRAM_NE1_Pin GPIO_PIN_7
#define PSRAM_NE1_GPIO_Port GPIOD
#define uSD_CLK_Pin GPIO_PIN_12
#define uSD_CLK_GPIO_Port GPIOC
#define uSD_D0_Pin GPIO_PIN_8
#define uSD_D0_GPIO_Port GPIOC
#define ARD_14_Pin GPIO_PIN_8
#define ARD_14_GPIO_Port GPIOG
#define STMOD_INT_Pin GPIO_PIN_6
#define STMOD_INT_GPIO_Port GPIOC
#define PSRAM_A3_Pin GPIO_PIN_3
#define PSRAM_A3_GPIO_Port GPIOF
#define PSRAM_A4_Pin GPIO_PIN_4
#define PSRAM_A4_GPIO_Port GPIOF
#define PSRAM_A5_Pin GPIO_PIN_5
#define PSRAM_A5_GPIO_Port GPIOF
#define I2C1_SDA_Pin GPIO_PIN_13
#define I2C1_SDA_GPIO_Port GPIOG
#define PSRAM_A14_Pin GPIO_PIN_4
#define PSRAM_A14_GPIO_Port GPIOG
#define PSRAM_A13_Pin GPIO_PIN_3
#define PSRAM_A13_GPIO_Port GPIOG
#define PSRAM_A15_Pin GPIO_PIN_5
#define PSRAM_A15_GPIO_Port GPIOG
#define ARD_15_Pin GPIO_PIN_7
#define ARD_15_GPIO_Port GPIOG
#define uSD_D1_Pin GPIO_PIN_9
#define uSD_D1_GPIO_Port GPIOC
#define PSRAM_A11_Pin GPIO_PIN_1
#define PSRAM_A11_GPIO_Port GPIOG
#define D7_Pin GPIO_PIN_10
#define D7_GPIO_Port GPIOE
#define USART3_RX_Pin GPIO_PIN_11
#define USART3_RX_GPIO_Port GPIOB
#define PSRAM_A18_Pin GPIO_PIN_13
#define PSRAM_A18_GPIO_Port GPIOD
#define PSRAM_A12_Pin GPIO_PIN_2
#define PSRAM_A12_GPIO_Port GPIOG
#define D1_Pin GPIO_PIN_15
#define D1_GPIO_Port GPIOD
#define D0_Pin GPIO_PIN_14
#define D0_GPIO_Port GPIOD
#define ARD_D0_Pin GPIO_PIN_0
#define ARD_D0_GPIO_Port GPIOC
#define ARD_D1_Pin GPIO_PIN_1
#define ARD_D1_GPIO_Port GPIOC
#define DF_CKOUT_Pin GPIO_PIN_2
#define DF_CKOUT_GPIO_Port GPIOC
#define PSRAM_A10_Pin GPIO_PIN_0
#define PSRAM_A10_GPIO_Port GPIOG
#define D6_Pin GPIO_PIN_9
#define D6_GPIO_Port GPIOE
#define D12_Pin GPIO_PIN_15
#define D12_GPIO_Port GPIOE
#define PSRAM_A17_Pin GPIO_PIN_12
#define PSRAM_A17_GPIO_Port GPIOD
#define PSRAM_A16_Pin GPIO_PIN_11
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

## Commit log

2022-10-27 comm 3d model
    [3DModelProject.kicad_pcb, 3DModelProject.kicad_sch]
2022-10-27 3d model
    [3DModelProject.kicad_pcb]
2022-11-17 Rev A files
    [Board.brd, Schematic.sch]
2022-11-17 lol, lmao even
    [EVCU.kicad_pcb, EVCU.kicad_sch]
2022-11-17 MCU caps
    [EVCU.kicad_sch]
2022-11-17 SWD and 3.3, 5V regs
    [EVCU Rev A BOM.xlsx, EVCU.kicad_sch]
2022-11-17 some more components
    [EVCU.kicad_sch, SN65HVD230.step]
2022-11-18 sd beginning
    [EVCU Rev A BOM.xlsx, EVCU.kicad_sch]
2022-11-18 please stop with the trello
    [EVCU.kicad_sch]
2022-11-18 schematic overview
2022-11-18 inductor rating
    [EVCU.kicad_sch]
2022-11-18 BOM stuff
    [EVCU Rev A BOM.xlsx]
2022-11-19 CANBUS esd
    [EVCU Rev A BOM.xlsx, EVCU.kicad_sch]
2022-11-19 120R resistor for CANH_L
    [EVCU.kicad_sch]
2022-11-19 esd protection
    [EVCU Rev A BOM.xlsx, EVCU.kicad_sch]
2022-11-20 EVCU BOM
    [EVCU Rev A BOM.xlsx, EVCU.kicad_sch]
2022-11-20 joe mamama
    [EVCU.kicad_sch]
2022-12-22 nom update
    [EVCU Rev A BOM.xlsx]
2023-01-10 jan 10 buck sd changes
    [EVCU Rev A BOM.xlsx, EVCU.kicad_pcb, EVCU.kicad_sch]
2023-01-18 finishing schematic
    [EVCU.kicad_sch]
2023-01-18 SCHEMATIC finish, connector footprint remaining
    [EVCU Rev A BOM.xlsx, EVCU.kicad_pcb, EVCU.kicad_sch]
2023-01-20 Not done some BSE connections and some footprints
    [EVCU.kicad_sch]
2023-01-20 basically done, start layout
    [EVCU.kicad_sch]
2023-01-20 should be done.
    [EVCU.kicad_sch]
2023-01-20 cap 1206 change, fuse, lin reg to 1117, testpoints, bom additions
    [EVCU Rev A BOM.xlsx, EVCU.kicad_pcb, EVCU.kicad_sch]
2023-01-24 accelerometer layout and op-amp footprint
    [EVCU.kicad_pcb, EVCU.kicad_sch]
2023-01-25 dcdc and filter layout
    [EVCU Rev A BOM.xlsx, EVCU.kicad_pcb, EVCU.kicad_sch]
2023-01-25 PCB layout for 1st iteration done, some labelling required
    [EVCU Rev A BOM.xlsx, EVCU.kicad_pcb, EVCU.kicad_sch]
2023-02-09 ur mom
    [EVCU.kicad_pcb, EVCU.kicad_sch]
2023-02-12 silkscreen and drc clean up
    [EVCU.kicad_pcb]
2023-02-13 added vref+ caps, fixed f1 via error, fixed gyro footprint, pcb ready for manufacturing
    [EVCU.kicad_pcb, EVCU.kicad_sch]
2023-02-13 bom. pcb. exports
    - updated bom added q1, some other capacitors. updated component costs
    - added logo to pcb
    - changed swd pins to female socket
    - exported gerbers
    - filled out digikey order form
    - filled out amazon order form
    [EVCU Rev A BOM.xlsx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]
2023-02-15 pcb and bom
    - moved mcu capacitors to top layer
    - rearranged components to shrink pcb
    - replaced j3 with 1x06 phoenix connector
    - replaced j6 with 1x02 male 2.54 header
    [EVCU Rev A BOM.xlsx, EVCU.kicad_pcb, EVCU.kicad_sch]
2023-02-15 more "final" changes
    - simulated and redid op amp voltage scaling for 0-5V to 0-3.3V sensors
    - decreased size of 3.3V copper pour
    - grounded pcb and db9 mounting holes
    - decreased size of board from 122x86 to 87x80 (in last commit but forgot to mention it)
    - moved swd zener diode to top layer, no more components on bottom layer
    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
    [EVCU Rev A BOM.xlsx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]
2023-02-15 parts order
    [EVCU.kicad_sch]
2023-02-15 cleaning up courtyard spacing
    [EVCU.kicad_pcb]
2023-02-16 gerbers again
    [EVCU-B_Cu.gbl, EVCU-B_Mask.gbs, EVCU-B_Paste.gbp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]
2023-02-22 software config - first flash
    [STM32_Test Debug.cfg]
2023-02-22 made 2 layer revision of pcb
    [EVCU 2 Layer BOM.xlsx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]
2023-02-22 微型 USB 到 USB
2023-02-26 2 layer gerbers
    [EVCU-B_Cu.gbl, EVCU-B_Mask.gbs, EVCU-B_Paste.gbp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]
2023-02-28 adc set - not done shutting off peripherials
2023-03-01 moving vias from pads
    [EVCU.kicad_pcb, EVCU.kicad_sch]
2023-03-02 increasing net clearance, changing trace angles, decreasing trace-to-pad width
    [EVCU.kicad_pcb]
2023-03-02 converted 2l to 4l
    [EVCU 2 Layer BOM.xlsx, EVCU Rev A BOM.xlsx, EVCU Rev B BOM.xlsx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]
2023-03-06 4 layer finished, gnd vias
    [EVCU-B_Cu.gbl, EVCU-B_Mask.gbs, EVCU-B_Paste.gbp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]
2023-03-07 fixed some silkscreen shit
    [EVCU.kicad_pcb]
2023-03-08 project initialized - added FATFS - RTOS - initialized 2 threads, 1 mutex, and added 1 adc data collection function
2023-03-08 added CAN as a folder - added adc buffer func
2023-03-09 final PCB submission
    [EVCU-B_Cu.gbl, EVCU-B_Mask.gbs, EVCU-B_Paste.gbp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]
2023-03-13 moved ADC Task over and initialized header.h
2023-03-16 deleted duplicated library files for some reason.
    added SD_task read/write functions and fixed up ADC_task
    [adc_task.c, main.c, main.h]
2023-03-25 working ADC samples
2023-03-25 adc works now, lmao
2023-03-27 adc works, controller.c framework set up ish
2023-03-27 adc works, controller.c framework set up, SD card code not tested until hardware arrives
2023-03-27 sd sample works
2023-04-06 ioc changes for the MCU - so changes in clk, pin config...etc

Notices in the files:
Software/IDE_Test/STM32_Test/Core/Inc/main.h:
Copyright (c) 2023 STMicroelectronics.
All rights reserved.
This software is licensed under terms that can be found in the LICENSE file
